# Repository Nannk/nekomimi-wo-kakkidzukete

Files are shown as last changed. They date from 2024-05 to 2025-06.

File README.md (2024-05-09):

# 猫耳を活気づけて ("Animated Cat Ears")

## TODO List
### new
  - [x] 1. Switch to eps8266-rtos-sdk :skull:
    - [x] 1.1. merge new project with the old repo(stop using platformio, use idf.py instead).
    - [x] 1.2. determine what components i need to implement.
  - [ ] 2. Implement components
    - [x] 2.1. Poses (see poses.cpp)
    - [x] 2.2. Servo output (PWM)
    - [ ] 2.3. SPI
    - [ ] 2.4. FFT
    - [ ] 2.5. That Magic part of pose selection i still have no idea how to implement
    - [ ] 2.6. Kalman Filter
    - [ ] 2.7. Attitude + Gyroscope rotation to angle adjustment
    - [ ] 2.8. \[optional\] Add thermometer or utilise the built-in one for temperature-dependent reactions
  - [ ] 3. Hardware 
    - [ ] 3.1. Find a way to fix Axles (Büroklammern) in place
    - [ ] 3.2. Wire second AMS1117 on the prototyping board
    - [ ] 3.3. Model all the hardware into the CAD project
    - [ ] 3.4. Make a board in KiCAD (most definitely for a PCB manufacturer)
    - [ ] 3.5. Decide on the Fur
  - [ ] 4. Misc
    - [ ] 4.1. Clean up README (make it actually readable)

### old
- [ ] Hardware 
  - [x] general structure (Hinges, servo placement and Head-to-ears connection) - still have to think where to put that paperclip wire.
  - [ ] Microcontroller & IMU
    - [x] Choose the IMU and MCU - it looks like ESP8266 has not enough umpf to read data, do 3 ffts on that data and send the result to serial. I want to use RPi0W and ESP8266, as RPi has only 2 PWM outputs. 
      - MCU: NodeMcuv2 (ESP8266) for servo control, RPi0W for data processing.
      - IMU: GY-91 IMU Board through SPI (MPU9250, BMP280) 6 Axis Gyro+Accelerometer, 3 Axis Magnetometer AK8963, Temperature and Pressure sensor BMP280
    - [x] change Voltage regulator to ams1117 
    - [ ] Make a power distribution board (2 ams1117 in parallel for 3 small servos)
    - [ ] Model all hardware into the Project (uncluding headband, CU usw)
  - [ ] Fluff (Fur) - [this?](https://www.amazon.de/WLLHYF-zotteligen-flauschige-Stuhlabdeckung-Weihnachten/dp/B0BJKKF45H) (a combination of white & black? pink insides?)

- [ ] Software
  - [x] Poses 
    - [x] List of poses 
    - [x] Poses as map of pose codes to desired_angle variables.
  - [x] IMU Data
    - [x] Find a Library (depends on hardware IMU)
      - [hideakitai/MPU9250](https://github.com/hideakitai/MPU9250) - with what appears to be a Kalman Filter.
      - [MPU9250_asukiaaa](https://github.com/asukiaaa/MPU9250_asukiaaa) - Library that can return raw data, i am using it right now.
    - [x] Get raw IMU data
    - [ ] Kalman Filter for attitude aquisition (there was already a lib for that, might just use it. although i need raw data for FFT)
    - [ ] How to detect the direction of a movement? From averaged Kalman Filter data?
  - [ ] IMU Data processing
    - [x] FFT  
    - [ ] IMU Data samples to compare to
    - [ ] Temperature and/or dTemp/dTime dependent reactions?

## 1.2.1 RTOS Task graph
```mermaid
graph TD;
A[Task: 
  Read data from SPI] -- IMU data --> B[Task: 
  Perform FFT];
A -- IMU data--> C[Task: 
  use Kalman Filter];
B -- Peaks: 
Magnitude, Frequency --> D[Task: 
  decide on Pose
  choose_pose
  adjust angles]
C --Attitude--> D;
A -- IMU data--> D;
D --servo angles--> E[Task:
  set pwm duty];
```

## 1.2.2 Compute schema
```mermaid
graph TD;
A[Accelerometer] --> KF[[Kalman Filter]] ;
KF --> C[Attitude];
B[Gyroscope] --> KF;

C --> D[Attitude dependent Position];
B --> E[Response to Rotation];
D --> F[Ear::set_ear_position];
E--> F;
F --> G[Ear::move_to_set_angles];

A --FFT--> I[Acceleration Spectrum];
I --> J[Determine Peaks and their Magnitude];
B --FFT--> K[Rotation Spectrum];
K --> L[Determine Peaks and their Magnitude];
L --> M[Compare with predefined Values];
J --> M;
M --> N[choose_pose];
N --> G;
```

## 2.1 List of poses
```text
 # | pose                               | ear left            | ear right           |
   | direction | opennnes               | left | main | right | left | main | right |
---|-----------|------------------------|---------------------|---------------------|
20 | sides     | fully open             | 106  | 90   | 26    | 106  | 90   | 26    |
21 | sides     | fully closed           | 0    | 90   | 132   | 0    | 90   | 132   |
22 | sides     | half open              | 53   | 90   | 79    | 53   | 90   | 79    |
23 | sides     | half closed to forward | 132  | 90   | 132   | 0    | 90   | 0     |
24 | sides     | half closed to back    | 0    | 90   | 0     | 132  | 90   | 132   |
---|-----------|------------------------|---------------------|---------------------|
10 | forward   | fully open             | 106  | 30   | 26    | 106  | 150  | 26    |
12 | forward   | half open              | 53   | 30   | 79    | 53   | 150  | 79    |
13 | forward   | half closed to inside  | 132  | 30   | 132   | 0    | 150  | 0     |
14 | forward   | half closed to outside | 0    | 30   | 0     | 132  | 150  | 132   |
---|-----------|------------------------|---------------------|---------------------|
31 | back      | fully closed           | 0    | 180  | 132   | 0    | 0    | 132   |
33 | back      | half closed to inside  | 0    | 180  | 0     | 132  | 0    | 132   |
34 | back      | half closed to outside | 132  | 180  | 132   | 0    | 0    | 0     |
---|-----------|------------------------|---------------------|---------------------|
and some intermediates
```
Note:
First digit: Ears direction
  - 1 - Forward
  - 2 - Sides 
  - 3 - Back

Second digit: Ears opennnes
  - 0 - fully open 
  - 1 - fully closed
  - 2 - half open
  - 3 - half closed to inside
  - 4 - half closed to outside

## 3.3 [CAD Model](https://cad.onshape.com/documents/12e9aba77e87c6321bec619e/w/794df45025b857e20fcdd77e/e/3349def638c04338ac328868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)

### servos
#### 2g servos
Brand:Surpass Hobby
S0002P 2g plastic gear digital servo
Voltage: 3.7\~4.2V DC
Torque *:≥0.4kgf·cm at 4.2V
Speed * : ≤0.06sec/60° at 4.2V
Operating Angle: 180°±10°(500\~2500μs)
Mechanical limit Angle: 360°
Weight: 2.2 g
Size: 16.7 × 8.2 × 17mm
Shell material: ABS
Motor type: hollow cup motor

#### 9g servos
TowerPro sg90 (i guess knock-offs)

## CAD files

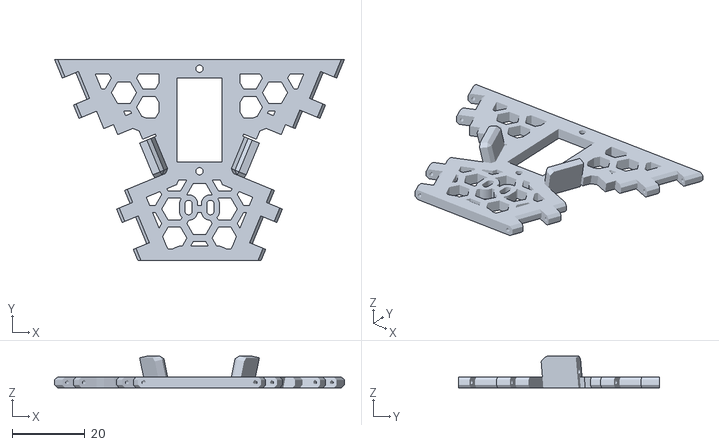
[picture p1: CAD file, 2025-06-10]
Models/v2/Bottom - Bottom.stl
79.8 x 55.4 x 8.73

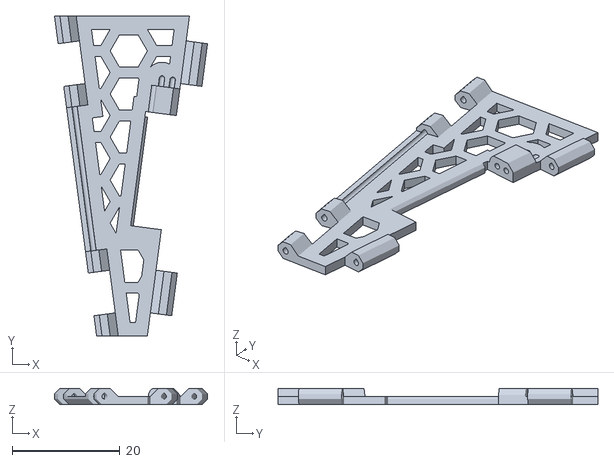
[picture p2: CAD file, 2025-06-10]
Models/v2/Side-Left - Left.stl
28.5 x 59.5 x 3.00

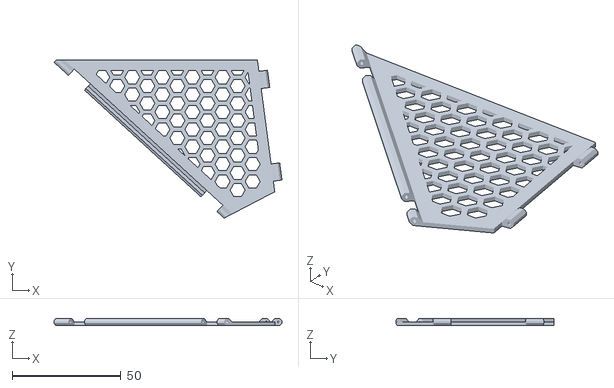
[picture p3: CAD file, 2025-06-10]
Models/v2/Top-Right - Top Right.stl
105.0 x 72.9 x 3.00

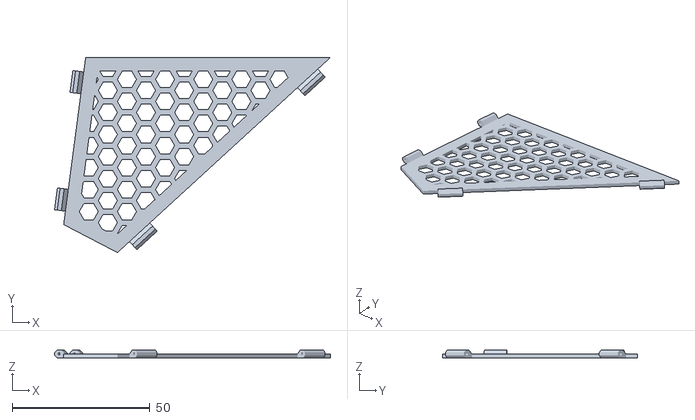
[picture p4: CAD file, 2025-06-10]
Models/v2/Top-Left - Top Left.stl
100.2 x 70.9 x 3.00

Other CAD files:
Models/v2/Side-Right - Right.stl

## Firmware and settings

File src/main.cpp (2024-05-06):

#include "Config.cpp"
#include "Ear.h"
#include "HardwareSerial.h" // Debug and data output
#include "poses.h" // Probably should rename to functions and move any misc functions there
#include <Arduino.h>
#include <MPU9250_asukiaaa.h> //mpu
#include <Wire.h>             //mpu und oled
#include <arduinoFFT.h>       //fft
#include <cstdlib>

// Variables
Ear leftear;
Ear rightear;

int pose_number = 31;

// mpu
MPU9250_asukiaaa mpu;
float aX, aY, aZ, rateX, rateY, rateZ, mpuTemperature;
float corr_gyroX, corr_gyroY, corr_gyroZ, corr_aX, corr_aY, corr_aZ;

// fft
const uint16_t samples = 64;
const double sampling_frequency = 500;

float pitch_vReal[samples];
float pitch_vImag[samples];
float yaw_vReal[samples];
float yaw_vImag[samples];
float roll_vReal[samples];
float roll_vImag[samples];

ArduinoFFT<float> pitch_fft =
    ArduinoFFT<float>(pitch_vReal, pitch_vImag, samples, sampling_frequency);
ArduinoFFT<float> yaw_fft =
    ArduinoFFT<float>(pitch_vReal, pitch_vImag, samples, sampling_frequency);
ArduinoFFT<float> roll_fft =
    ArduinoFFT<float>(pitch_vReal, pitch_vImag, samples, sampling_frequency);

// Adafruit_SSD1306 oled(SCREEN_WIDTH, SCREEN_HEIGHT, &Wire, -1);

unsigned long previosmillis = 0;

// possible calibration values because gyro has an offset, so it drifts quite
// heavily and accel has an offset too
void calibration() {
  corr_gyroX = -1.647184035;
  corr_gyroY = 0.7031929047;
  corr_gyroZ = -0.4409756098;
  corr_aX = 0.00711751663;
  corr_aY = 0.05541019956;
  corr_aZ = 0.1359201774;
}

void mpusetup() {
  Wire.begin();
  Wire.setClock(400000UL);

  mpu.beginGyro(GYRO_FULL_SCALE_500_DPS);
  // mpu.beginAccel();
}

// main thingy
void setup() {
  leftear.earsetup(LLEFTWINGPIN, LMAINAXISPIN, LRIGHTWINGPIN);
  rightear.earsetup(RLEFTWINGPIN, RMAINAXISPIN, RRIGHTWINGPIN);

  /*
   * Most definitely wont need this code anymore, its for i²c oled.
  if (!oled.begin(SSD1306_SWITCHCAPVCC, 0x3C)) {
    while (true)
      ;
  }
*/

  calibration();
  mpusetup();

  Serial.begin(576000);
  previosmillis = millis();
}
/*
 * a wrapper around fft functions that computes fft and returns major peak.
 */
void perform_fft(ArduinoFFT<float> fft) {
  fft.dcRemoval();
  fft.windowing(FFTWindow::Rectangle, FFTDirection::Forward); // Weigh data
  fft.compute(FFTDirection::Forward);                         // Compute
  fft.complexToMagnitude(); // Compute magnitudes
}

void loop() {

  if (millis() - previosmillis >= 10) { // cap update @ 100Hz
    // get a frame of gyroscope data
    for (int i = 0; i < samples; i++) {
      while (mpu.gyroUpdate() != 0) {
        delay(1); // i dont like it. Should parallelize waiting for data and
                  // computing fft for previous data.
      }
      pitch_vReal[i] = mpu.gyroY() + corr_gyroY; // rateY
      roll_vReal[i] = mpu.gyroX() + corr_gyroX;  // rateX
      yaw_vReal[i] = mpu.gyroZ() + corr_gyroZ;   // rateZ

      pitch_vImag[i] = 0.0; // clear previous data
      roll_vImag[i] = 0.0;
      yaw_vImag[i] = 0.0;

      // rateY = mpu.gyroY() + corr_gyroY;
      // rateZ = mpu.gyroZ() + corr_gyroZ;
    }

    perform_fft(pitch_fft);
    perform_fft(roll_fft);
    perform_fft(yaw_fft);

    for (int i = 0; i < samples / 2; i++) {
      Serial.print(pitch_vReal[i]);
      Serial.print(",");
      Serial.print(roll_vReal[i]);
      Serial.print(",");
      Serial.print(yaw_vReal[i]);
      Serial.print(";");
    }
    Serial.println("");
    /*
    for (float real : pitch_vReal) {
      Serial.print(real);
      Serial.print(";");
    }
    Serial.println("");
    */

    previosmillis = millis();
  }
  /*
   * Neiter this code, but ill leave it here for now.
  oled.clearDisplay();
  for (int i = 0; i < (samples / 2) - 1; i++) {
    oled.drawLine(i * 4, 0.1 * vReal[i], (i + 1) * 4, 0.1 * vReal[i + 1],
                  WHITE);
  }
  oled.setTextSize(1);
  oled.setTextColor(WHITE);
  oled.setCursor(68, 5);
  oled.println(fft.majorPeak());
  oled.display();
  */

  /*
  if (mpu.accelUpdate() == 0) {
    aX = mpu.accelX() + corr_aX;
    aY = mpu.accelY() + corr_aY;
    aZ = mpu.accelZ() + corr_aZ;
  }
  */

  // to move servos process what the anle should be,
  // use a "setter" function Ear::set_ear_position(int l, int m, int r)
  // then call Ear::move_to_set_angles() every 20ms (or 50ms) or so
}

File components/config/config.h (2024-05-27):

#pragma once

#ifndef Config_h
#define Config_h

#include <i2c.h>

// #define SCL D1
// #define SDA D2

// Left
#define LMAINPIN 0 // D3
//    wings
#define LLEFTWINGPIN 14  // D5
#define LRIGHTWINGPIN 12 // D6

// Right
#define RMAINPIN 2 // D4
//    wings
#define RLEFTWINGPIN 13  // D7
#define RRIGHTWINGPIN 15 // D8

#define MIN_MICROS 500
#define MAX_MICROS 2400

// TODO: set the correct values here
#define I2C_MASTER_SCL_IO 5 /*!< gpio number for I2C master clock */
#define I2C_MASTER_SDA_IO 4 /*!< gpio number for I2C master data  */
#define I2C_MASTER_NUM                                                         \
  I2C_NUM_0                         /*!< I2C port number for master dev        \
                                     */
#define I2C_MASTER_TX_BUF_DISABLE 0 /*!< I2C master do not need buffer */
#define I2C_MASTER_RX_BUF_DISABLE 0 /*!< I2C master do not need buffer */

#define MPU9250_SENSOR_ADDR 0x68   /*!< slave address for MPU9250 sensor */
#define MPU9250_CMD_START 0x41     /*!< Command to set measure mode */
#define MPU9250_WHO_AM_I 0x75      /*!< Command to read WHO_AM_I reg */
#define WRITE_BIT I2C_MASTER_WRITE /*!< I2C master write */
#define READ_BIT I2C_MASTER_READ   /*!< I2C master read */
#define ACK_CHECK_EN 0x1           /*!< I2C master will check ack from slave*/
#define ACK_CHECK_DIS 0x0 /*!< I2C master will not check ack from slave */
#define ACK_VAL 0x0       /*!< I2C ack value */
#define NACK_VAL 0x1      /*!< I2C nack value */
#define LAST_NACK_VAL 0x2 /*!< I2C last_nack value */

/**
 *  TODO: Define the mpu9250 register address:
 */
#define SMPLRT_DIV 0x19
#define CONFIG 0x1A
#define GYRO_CONFIG 0x1B
#define ACCEL_CONFIG 0x1C
#define ACCEL_XOUT_H 0x3B
#define ACCEL_XOUT_L 0x3C
#define ACCEL_YOUT_H 0x3D
#define ACCEL_YOUT_L 0x3E
#define ACCEL_ZOUT_H 0x3F
#define ACCEL_ZOUT_L 0x40
#define TEMP_OUT_H 0x41
#define TEMP_OUT_L 0x42
#define GYRO_XOUT_H 0x43
#define GYRO_XOUT_L 0x44
#define GYRO_YOUT_H 0x45
#define GYRO_YOUT_L 0x46
#define GYRO_ZOUT_H 0x47
#define GYRO_ZOUT_L 0x48
#define PWR_MGMT_1 0x6B
#define WHO_AM_I 0x75 /*!< Command to read WHO_AM_I reg */

#endif

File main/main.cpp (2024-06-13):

#include "config.h"
#include "ears.h"
#include "mpu.h"
#include <cstdint>
#include <esp_heap_caps.h>
#include <esp_log.h>
#include <esp_spi_flash.h>
#include <esp_task_wdt.h>
#include <esp_timer.h>
#include <freertos/FreeRTOS.h>
#include <freertos/task.h>
#include <gpio.h>
#include <stdio.h>
#include <uart.h>

static const char *TAG = "Main";

static Ears ears;
static Mpu mpu;
// mpu variables
uint8_t sensor_data[14];
uint8_t who_am_i, i;
double Temp;
int ret;
long long current_millis;
long long previous_millis;

void mpu_task(void *Parameters) {

  uart_set_baudrate(UART_NUM_0, 112500);

  // assign channels and start servos
  ears.ears_init({0, 1, 2, 3, 4, 5});
  // initialise i2c and mpu
  mpu.mpu9250_init(I2C_MASTER_NUM);

  ESP_LOGI(TAG, "done setting up");
  // ears.choose_pose(21);
  // ears.move_to_set_angles();
  // vTaskDelay(1000 / portTICK_RATE_MS); // for assembling wing correctly

  // test thing
  ears.choose_pose(31);
  ears.move_to_set_angles();
  previous_millis = esp_timer_get_time() / 1000;

  while (1) {

    // mpu.mpu9250_read(I2C_MASTER_NUM, WHO_AM_I, &who_am_i, 1);

    // memset(sensor_data, 0, 14);
    ret = mpu.mpu9250_read(I2C_MASTER_NUM, ACCEL_XOUT_H, sensor_data, 14);

    if (ret == ESP_OK) {
      // ESP_LOGI(TAG, "*******************");

      // for (i = 0; i < 14; i++) {
      ESP_LOGI(TAG, "%d, %d, %d, %d, %d, %d, %d, %d, %d, %d, %d, %d, %d, %d",
               (int16_t)(sensor_data[0]), (int16_t)(sensor_data[1]),
               (int16_t)(sensor_data[2]), (int16_t)(sensor_data[3]),
               (int16_t)(sensor_data[4]), (int16_t)(sensor_data[5]),
               (int16_t)(sensor_data[6]), (int16_t)(sensor_data[7]),
               (int16_t)(sensor_data[8]), (int16_t)(sensor_data[9]),
               (int16_t)(sensor_data[10]), (int16_t)(sensor_data[11]),
               (int16_t)(sensor_data[12]), (int16_t)(sensor_data[13]));
      //}

      // ESP_LOGI(TAG, "error_count: %d\n", error_count);
    } else {
      ESP_LOGE(TAG, "No ack, sensor not connected...skip...\n");
    }

    // ESP_LOGD(TAG, "memory: %d",
    // (int)heap_caps_get_free_size(MALLOC_CAP_32BIT));

    vTaskDelay(10 / portTICK_PERIOD_MS);
  }
  i2c_driver_delete(I2C_MASTER_NUM);
  fflush(stdout);
}

extern "C" void app_main() {
  xTaskCreate(mpu_task, "mpu_task", 2048, NULL, 10, NULL);
}

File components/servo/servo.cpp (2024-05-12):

/**
Copied and modified code from Achim Pieters | StudioPieters®
 **/

#include "servo.h"
#include "esp_log.h"
#include <array>
#include <cstdint>
#include <freertos/FreeRTOS.h>
#include <freertos/task.h>
#include <pwm.h>
#include <stdio.h>
#include <stdlib.h>
#include <uart.h>

static const char *TAG = "servo";

// servos use 500µs ~ 2500µs
uint16_t calc_duty_from_angle(int angle) {
  // return (0.025 + (0.1325 - 0.025) * (double)angle / 180) * UINT8_MAX;
  return ((2000 * (double)angle) / 180) + 500;
}

// initialise pwm
void Servo::servo_init() {
  ESP_LOGI(TAG, "initialising servos"); // debug
  pwm_init(5000, duties, 6, pins);
  pwm_set_phases(phases);
}

// function to run as a task
void rotate_task(void *input_data) {
  ESP_LOGD(TAG, "in create task");
  std::array<Parameters, 6> *data{
      reinterpret_cast<std::array<Parameters, 6> *>(input_data)};
  for (Parameters param : *data) {
    ESP_LOGD(TAG, "channel: %d angle: %d", param.channel, param.angle);
    pwm_set_duty(param.channel, param.angle);
  }
  pwm_start();
  // vTaskDelay(20 / portTICK_PERIOD_MS);
  //  pwm_stop(0x00);
  vTaskDelete(NULL);
}

// setter and task creator
void Servo::servo_rotate_to_angle(std::array<int, 6> &data) {

  for (int i = 0; i < 6; i++) {

    int *tmp = &data[i];
    persistent_params[i].angle = calc_duty_from_angle(*tmp);
    persistent_params[i].channel = i;
    ESP_LOGD(TAG, "in rotate to angle loop interation %d, data: %d", i,
             persistent_params[i].angle);
  }
  xTaskCreate(rotate_task, "rotate_task", 1024, &persistent_params, 5, NULL);
}

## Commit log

2023-12-30 esp8266 does not work with arduino servo library
2024-01-03 changed servo controls for testing purposes to use pots
2024-01-04 tested servo rotation and updated Readme
2024-01-04 still trying to solve multiple definition problem
    [Ear.cpp, main.cpp]
2024-01-04 i broke everythin again
    [main.cpp]
2024-01-05 well i forgot to but break in switch
2024-01-05 Main servos were inverted
2024-01-05 defined i2c pins
2024-01-05 changed IMUtoMCU communication to spi
2024-01-06 i2c it is. Also new servos dont like default esp8266 servo library
2024-01-06 servo specs
2024-01-06 started kicad schematic
    [nekomimi-wo-kakkidzukete.kicad_pcb, nekomimi-wo-kakkidzukete.kicad_sch]
2024-01-08 serial writes should be kept to a minimum, because it makes the servos start moving not at the same time
2024-01-09 imu working
2024-03-24 added crude calibration
2024-04-07 something with kicad mb and readme
    [nekomimi-wo-kakkidzukete.kicad_sch]
2024-05-04 fft is working, data output on an i2c display might have been a bad idea
2024-05-04 rewrote choose_pose to just set the angle instead of moving the servos
2024-05-05 made a flow chart describing what i need the code to do
2024-05-06 tidied the code a bit, removed display support, added ffts for pitch and yaw
2024-05-06 update comments, add correct platformio.ini file
    [main.cpp]
2024-05-07 servo support. compiles, panics
2024-05-07 servo library is written incorrectly, pwm_init initialises everything at once
2024-05-08 pwm is not kinda working
2024-05-09 fixed servo angles not being updated
    [main.cpp, servo.cpp]
2024-05-09 fixed memory leak caused by creating and not freeing the pointer in servo_rotate_to_angle
    [main.cpp, servo.cpp]
2024-05-09 better way of handling 2 voltage regulators
    [nekomimi-wo-kakkidzukete.kicad_sch]
2024-05-09 previous bugfix introduced more bugs, all but last channel had no pwm. Fixed thos bugs
    [servo.cpp]
2024-05-12 it suddenly started working correctly
    [main.cpp, servo.cpp]
2024-05-12 no idea what changed, i just opened kicad to check resistord values
2024-05-12 fixed one channel desynchronising from the others
    [ears.cpp, main.cpp, servo.cpp]
2024-05-27 i2c pullup does not work. mpu data is there though
    [main.cpp, mpu.cpp]
2024-06-13 nothing really changed, still not working
    [main.cpp]
2025-06-10 stl files because onshape does not allow export
    [Bottom - Bottom.stl, Side-Left - Left.stl, Side-Right - Right.stl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]
